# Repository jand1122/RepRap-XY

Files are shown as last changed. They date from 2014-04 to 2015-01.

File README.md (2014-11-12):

This is the first release of a RepRap-XY 3D printer. It is based on the excellent design of Zelogik. See his github archive at:  https://github.com/zelogik/AluXY

His design and my variant are discussed in the RepRap forum at:: http://forums.reprap.org/read.php?4,297740

When I saw this printer I thought, this is the printer I want. It has all the features I want in a printer:

- Based on the Core-XY system. (see http://corexy.com/theory.html)
- Frame made from aluminium extrusions.
- No motors, belts and guides on the outside of the frame.

It only has one problem for me, it is made from CNC-ed aluminium and I do not have access to a CNC machine.
I decided to build a printer based on this design, but use printed parts instead of aluminium parts. That is what you will find here.

This is a work in progress, Use at your own risk.

I made one and it is working just fine.
I did not yet make something for the X and Y endstops.
A simple adjustable Z endstop exists and does the job for adjusting the first layer height.

The file src/RepRap-XY.FCStd is the complete assembly in FreeCAD format.
The file src/RepRap-XY.vc3 is the complete assembly in VIACAD format.

The file build.py will mirror a few parts and generate the STEP and STL files.
Just open the file in FreeCAD and run a a macro.

In the doc folder you will find a BOM. This BOM is not generated from the model but hand made, so be carefull
You will not (yet?) find build instructions there.  Have a look at the sourcefile RepRap-XY.FCStd (FreeCAD) and RepRap-XY.vc3 to see how everything fits together.

To see some videos of my printer have a look at my youtube channel: https://www.youtube.com/channel/UCOyTdQOCCLdy45FtSlam_3A/feed
and some images at my imgur album: http://jand1122.imgur.com/

Have fun.

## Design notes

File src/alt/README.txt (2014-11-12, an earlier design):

You will find alternative parts here:

belt-clamp_v2 by peterv3210

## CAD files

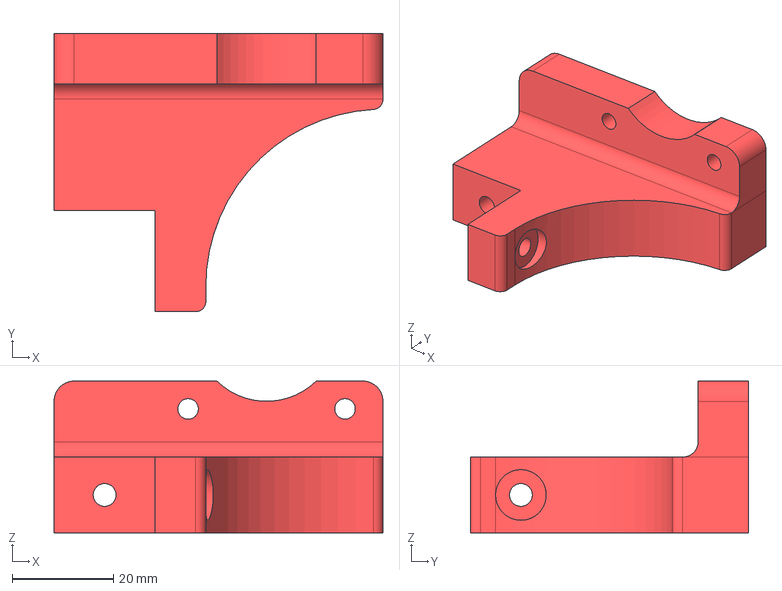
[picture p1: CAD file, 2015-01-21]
src/Z-motor-mount.FCStd
65.0 x 55.0 x 30.0 mm

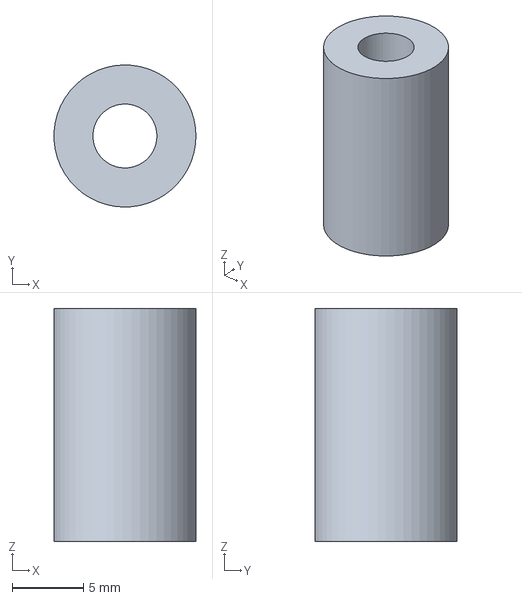
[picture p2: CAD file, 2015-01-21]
step/spacer-16mm4.step
9.99 x 10.00 x 16.4 mm

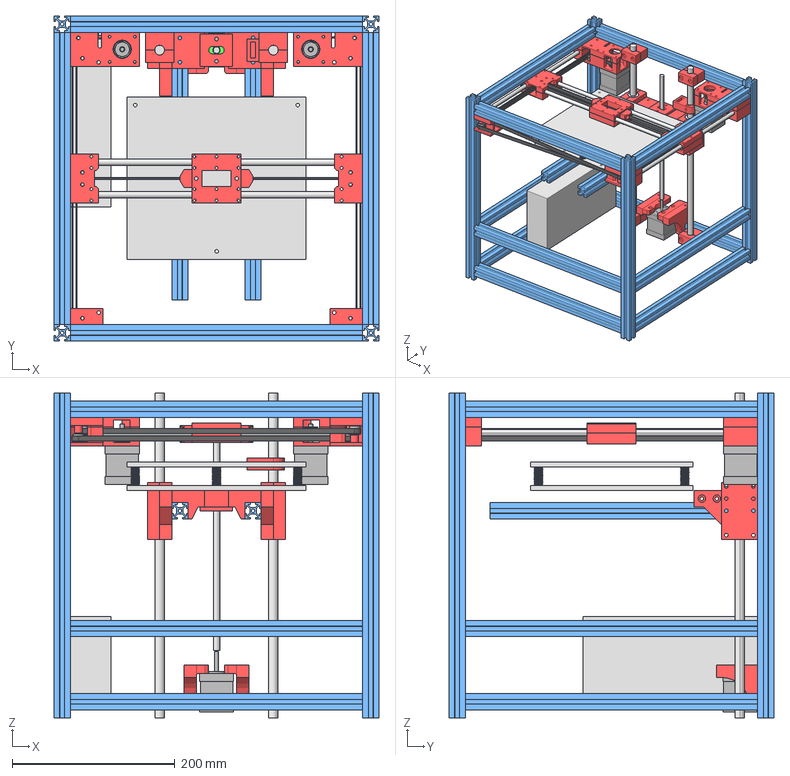
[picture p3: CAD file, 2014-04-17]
test/RepRap-XY-upsidedown-Z.FCStd
400.0 x 400.0 x 400.0 mm
Nema-17
Nema-018
Nema-019
Power_supply
F624zz-bearing
624-bearing
spacer-1
F624zz-bearing001
624-bearing001
washer-M4
washer-M005
F624zz-bearing002
624-bearing002
washer-M006
washer-M007
F624zz-bearing003
624-bearing003
washer-M008
washer-M009
F624zz-bearing004
624-bearing004
washer-M010
washer-M011
washer-M012
washer-M013
F624zz-bearing005
624-bearing005
spacer-002
washer-M014
washer-M015
F624zz-bearing006
624-bearing006
spacer-003
washer-M016
washer-M017
F624zz-bearing007
624-bearing007
spacer-004
washer-M018
washer-M019
F624zz-bearing008
624-bearing008
washer-M020
washer-M021
F624zz-bearing009
624-bearing009
washer-M022
washer-M023
F624zz-bearing010
624-bearing010
washer-M024
washer-M025
F624zz-bearing011
624-bearing011
washer-M026
washer-M027
smooth-bar-12x400
Alu-20x20x360
Alu-20x20x361
Alu-20x20x362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

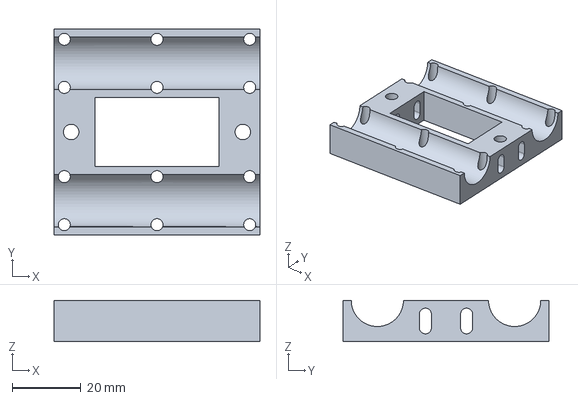
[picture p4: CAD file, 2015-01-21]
step/carriage.step
60.0 x 60.0 x 12.0 mm

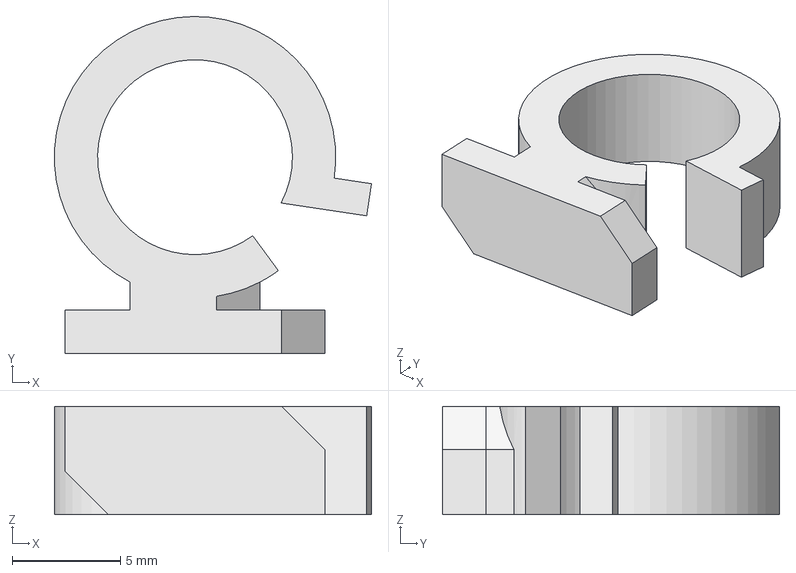
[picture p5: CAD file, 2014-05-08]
src/cable-guide.FCStd
14.6 x 15.6 x 5.00 mm

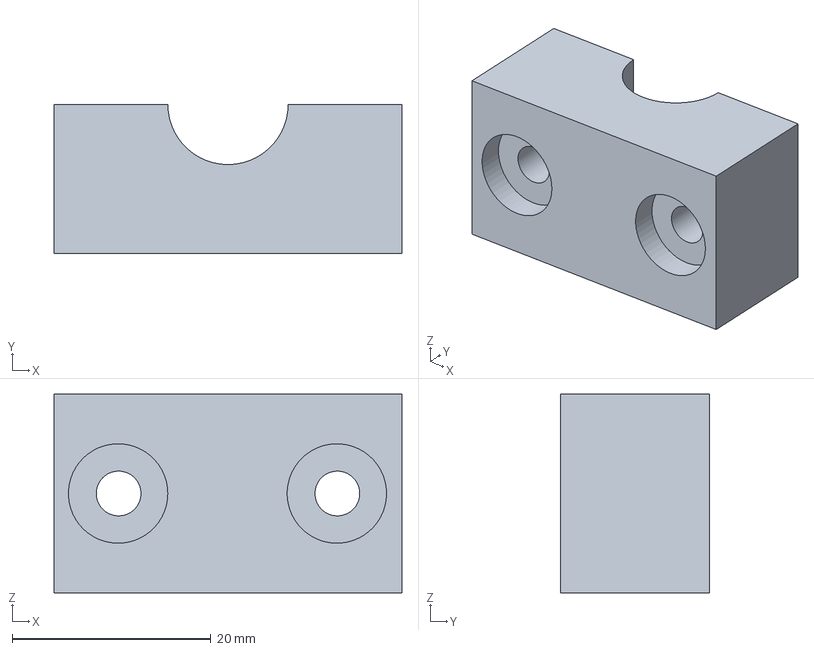
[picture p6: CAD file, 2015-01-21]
step/Z-axis-clamp-2.step
35.0 x 15.0 x 20.0 mm

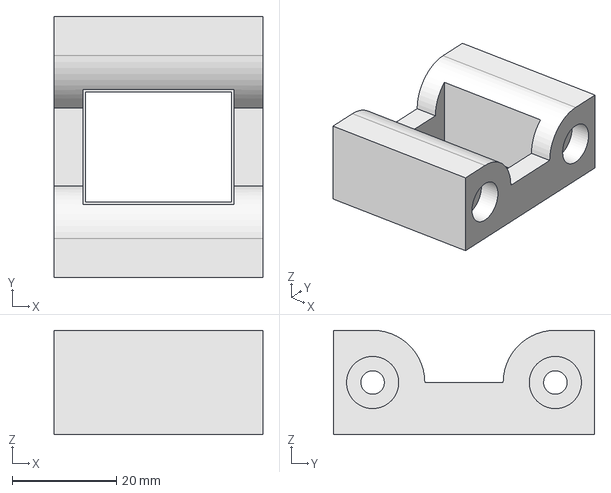
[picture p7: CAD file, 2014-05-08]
src/power-plug-mount.FCStd
40.0 x 50.0 x 20.0 mm

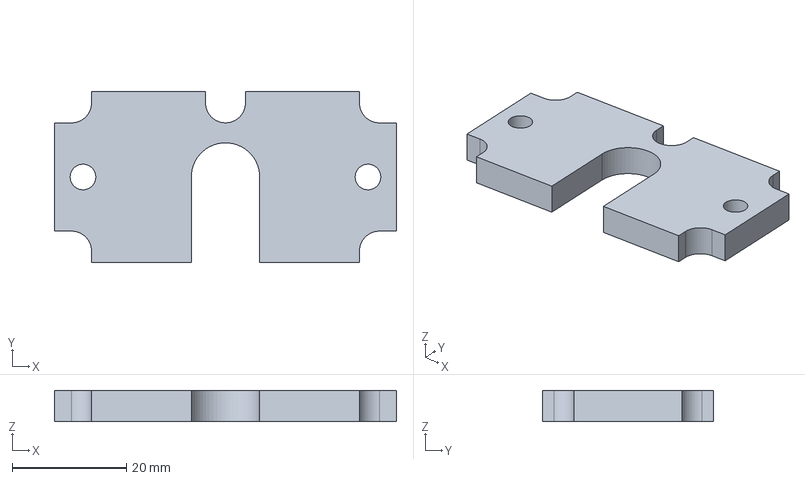
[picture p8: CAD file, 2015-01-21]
step/e3d-mount-2.step
60.0 x 30.0 x 5.50 mm

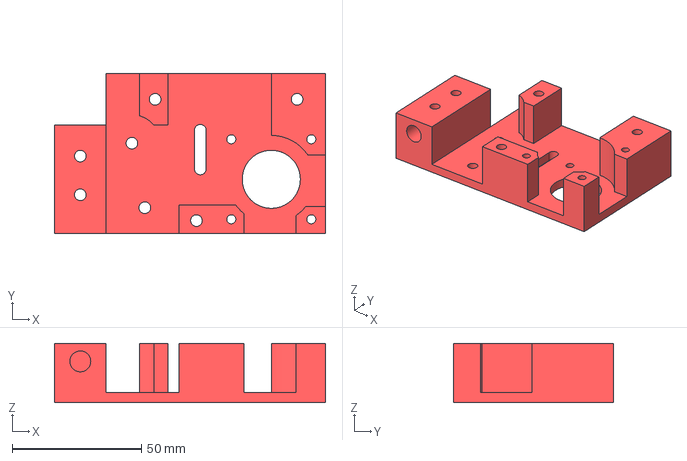
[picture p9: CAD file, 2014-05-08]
src/motor-block.FCStd
105.0 x 62.0 x 23.0 mm

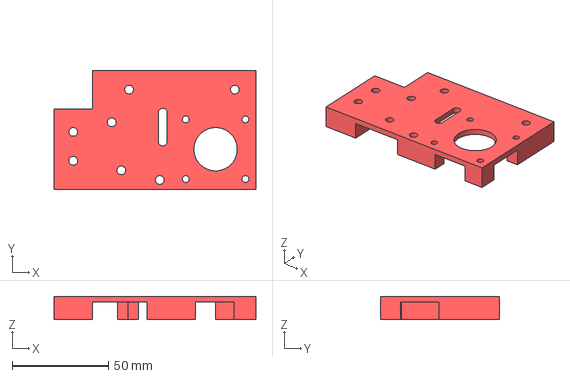
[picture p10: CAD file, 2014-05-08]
src/motor-block-top.FCStd
105.0 x 62.0 x 12.0 mm

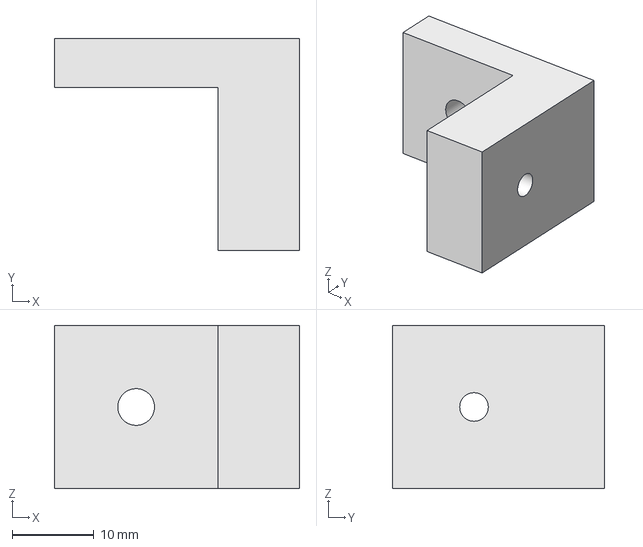
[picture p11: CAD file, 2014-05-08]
src/PS-mount.FCStd
30.0 x 26.0 x 20.0 mm

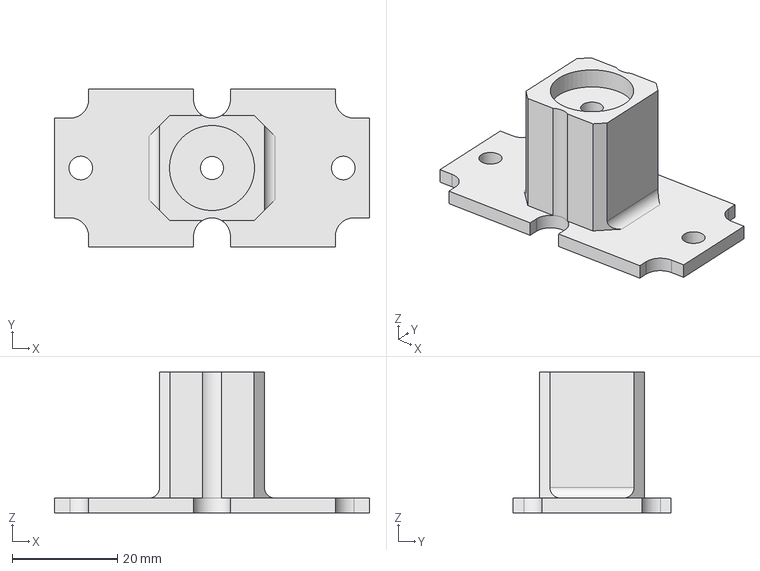
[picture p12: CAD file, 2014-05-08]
src/e3d-mount-1.FCStd
60.0 x 30.0 x 26.8 mm

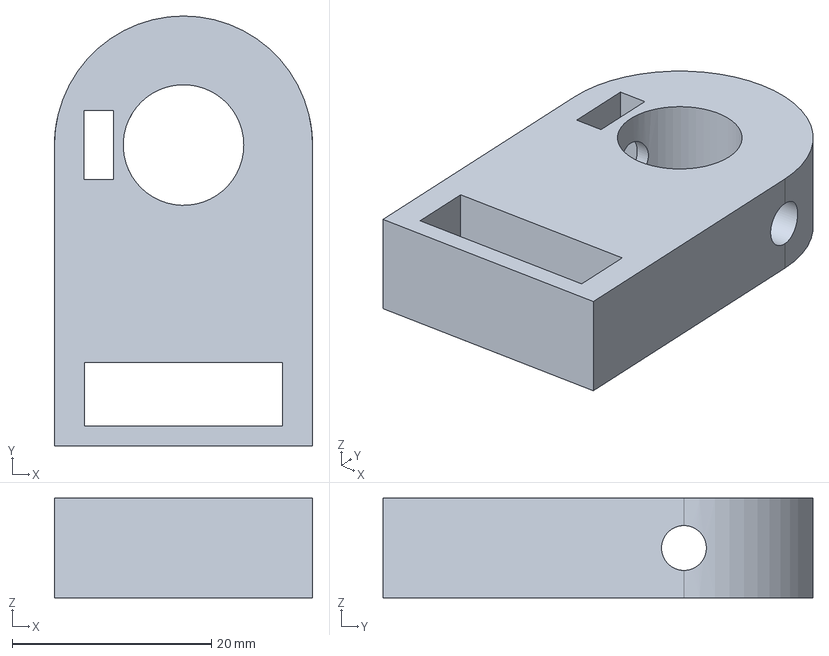
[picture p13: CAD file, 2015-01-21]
step/Z-endstop-mount.step
25.9 x 43.1 x 10.0 mm

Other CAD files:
src/RepRap-XY.FCStd
step/Z-motor-mount-mirrored.step
step/motor-block.step
src/power-switch-mount.FCStd
step/motor-block-top-mirrored.step
src/RAMPS-mount-1.FCStd
src/RAMPS-mount-2.FCStd
src/XY-block-top.FCStd
src/XY-block.FCStd
src/Z-axis-clamp-1.FCStd
src/Z-axis-clamp-2.FCStd
src/Z-block-1.FCStd
src/Z-block-2.FCStd
src/Z-endstop-adjust.FCStd
src/Z-endstop-mount.FCStd
src/Z-leadscrew-bearing-block.FCStd
src/Z-nut-1.FCStd
src/Z-nut-2.FCStd
src/Z-nut-3.FCStd
src/Z-nut-4.FCStd
src/alt/belt-clamp_v2.FCStd
src/belt-clamp.FCStd
src/carriage.FCStd
src/e3d-mount-2.FCStd
src/idler-block-top.FCStd
src/idler-block.FCStd
src/spacer-16mm4.FCStd
src/spacer-7mm.FCStd
src/spacer-9mm4.FCStd
src/washer-M4.FCStd
step/PS-mount.step
step/RAMPS-mount-1.step
step/RAMPS-mount-2.step
step/XY-block-top.step
step/XY-block.step
step/Z-axis-clamp-1.step
step/Z-block-1-mirrored.step
step/Z-block-1.step
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

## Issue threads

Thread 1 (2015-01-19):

Z Axis

jvegaf, 2015-01-19:
Hi, first of all, congratulations for you awesome work !!!!

I'm thinking fork you repo and do a few changes

do you know what will happens I try change 12 mm smooth bar by a 8mm smooth bar on Z Axis ?

(I have a 2  8mm smooth bar prepared for Z axis)

Thanks

jand1122, 2015-01-20:
Hi Jose,

Thanks, for the compliment. I think it is not really difficult to change it
to 8mm rods for the Z-axis, but I think it is not a good idea. the 12mm
rods are much stiffer than 8 mm rods. I think you will get to much flex in
the bed. I would recommend to get some 12 mm rods.

Best regards,

Jan

2015-01-19 3:23 GMT+01:00 Jose Vega <notifications@github.com>:

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

Closed 2015-01-21.

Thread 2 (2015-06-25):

Z-Axis Assembly

chrisdauria, 2015-06-25:
Hi Jand,

I am in the process of building your version of this printer and I am not sure how the inside of where the leadscrew and the bed come together goes. In other words how do you keep both nuts in position in that little enclosure? Thanks for your help!

Chris

Closed 2016-04-09.

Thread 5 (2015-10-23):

Printer belt construction

dragondgold, 2015-10-23:
Hi! I'm starting to build this printer and I'm having some problems to put the belts. I have read the forum but couldn't find a clear diagram about how to put the belts and how the tension system works. Would you mind taking a picture inside where the motors are mounted?

g2david, 2015-10-23:
There exists an adjustable bearing next to the motor mount

dragondgold, 2015-10-23:
@g2david yes, I can see it. But how do you put the belts inside? I can't find any diagram or image and I can't tell from your pictures what bearings, pulley and spacers to put inside

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

g2david, 2015-10-23:
Let me t
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

g2david, 2015-10-23:
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

g2david, 2015-10-23:
If you start with the X Carriage, It is quite easy to pass through

Otherwise, You need to have patient to fish the belt inside the XY blocks. It takes me 30 mins. I use a dummy belt to fish the belt out of the blocks.  Sweating

dragondgold, 2015-10-23:
Thank you very much! Great printer btw :)

Closed 2015-10-23.

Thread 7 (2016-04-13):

How do these belt clips hold? They seem not to have perpendicular traction on the belts.

brunobasto, 2016-04-13:
Congrats on the project! I've seen the videos. It looks awesome!

jand1122, 2016-04-13:
Both clips on the right side are with the open side up, so the traction is at the front, the smooth side at the back. At the left side the open side is down, so the traction is also at the front and the smooth side at the back

Just slide the belt from the open side into the clip. (Single, do not fold the beld) You have to cut the belts to length within a few teeth accurate. Tensioning is done in the motor blocks. It is strong enough. it has never failed in over a yesr of printing many kg of ABS plastic.

brunobasto, 2016-04-13:
Awesome! Good to know.

Thank you

Closed 2016-04-13.

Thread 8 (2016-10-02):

How ist the Z Axis fixed to the Printbed?

MrKingofRome, 2016-10-02:
Im on my way of buildung your Printer design, and now stumbled upon the Problem, how the Z Axis is fixes to the printbed, and if it is easily interchangeable to Tr10x2 Leadscrews.

Looking Forward to hear from you,

Greetings from Germany

jand1122, 2016-10-03:
Two nuts are hold by  Z-nut-1. This can slide left-right in Z-nut-2. Z-nut-4 goes on top of that.
This assembly can slide foreward and backbards between two Z-nut-3 parts.

This gives a Z-wobble compensation.

When you can fit the TR-10 nut in Z-nut-1 it is simple to change. Otherwise you have to redesign Z-nut-1,2 and 4.

You can check the complete assembly in step/RepRap-XY.step or src/RepRap-XY.FCStd

Hope this helpsGreetings from the Netherlands

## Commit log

2014-03-30 First public release
    [XY-block-top.FCStd, XY-block.FCStd, Z-axis-clamp-1.FCStd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]
2014-04-03 Changed Z motor back to top
    [Z-motor-mount.FCStd]
2014-04-06 Added build.py script to create STEP and STL file
2014-04-06 Aligned some parts for easy printing
    [XY-block-top.FCStd, Z-block.FCStd, carriage-old.FCStd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]
2014-04-06 Addes STEP files
    [XY-block-top.step, XY-block.step, Z-axis-clamp-1.step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]
2014-04-06 Addes STL Files
    [XY-block-top.stl, XY-block.stl, Z-axis-clamp-1.stl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]
2014-04-06 Updated core-XY.FCStd and core-XY.stp files
    [core-XY.FCStd]
2014-04-12 Some updates on Z-axis, renamed core-XY to RepRap-XY
    [RepRap-XY.FCStd, XY-block-top.step, XY-block.step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]
2014-04-17 Updated Z-axis
    [XY-block-top.step, XY-block.step, Z-axis-clamp-1.step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]
2014-04-17 Update Z-axis and regenerate STEP/STL files
    [RepRap-XY.FCStd, XY-block-top.step, XY-block.step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]
2014-04-17 Upsidedown
    Just a test to see if you can use the Z-axis upsidedown
    [RepRap-XY-upsidedown-Z.FCStd]
2014-04-20 Added a few parts
    [RAMPS-mount-1.FCStd, RAMPS-mount-1.step, RAMPS-mount-1.stl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]
2014-05-08 Added a few more parts
    [PS-mount.FCStd, PS-mount.step, PS-mount.stl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]
2014-05-10 updated assembly
    [RepRap-XY.FCStd]
2014-05-10 Added BOM
    [BOM.ods]
2014-05-10 Added BOM.pdf
2014-05-12 Updated BOM
    [BOM.ods]
2014-05-25 Update BOM
    [BOM.ods]
2014-07-28 rebuild STEP, STL added marlin.zip
    STEP and STL files regenerated and added marlin.zip configured for
    core-xy
    [PS-mount.step, PS-mount.stl, RAMPS-mount-1.step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]
2014-09-01 Update values M3 and M4
    The values of the M3 and M4 parts were shifted by one line
    [BOM.ods]
2014-09-01 Just another update in BOM.ods
    [BOM.ods]
2014-11-12 Added alternative belt_clamp by peterv3210
    Added an alternative belt_clamp made by peterv3210 and added alt
    folders. Also regenerated the STL and STEP files
    [PS-mount.step, RAMPS-mount-1.step, RAMPS-mount-2.step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]
2015-01-20 Changed z-motor-mount
    Changed z-motor-mount and updated step/stl files
    [PS-mount.step, RAMPS-mount-1.step, RAMPS-mount-2.step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]
2015-01-21 Selected last Item in Z-motor-mount
    Selected last Item in Z-motor-mount and regenerated STL and STEP
    [PS-mount.step, RAMPS-mount-1.step, RAMPS-mount-2.step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]
